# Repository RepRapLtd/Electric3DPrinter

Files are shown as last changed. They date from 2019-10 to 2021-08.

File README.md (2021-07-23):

The RepRap Ltd Electric 3D Printer
==================================

This document is a log of a RepRap Ltd ongoing research project to create a completely new type of 3D printer invented by [Adrian Bowyer](https://reprapltd.com/about/) (to whom “I” below refers…).

(All the images here are in the Pix directory of this repository.)

The Initial Invention (25 July 2019)
------------------------------------

The invention combines three ideas to make a fourth.  The three are:

1.  The [reverse-CT scan 3D printing technique](https://3dprintingindustry.com/news/uc-berkeley-researchers-develop-a-projection-based-3d-printer-from-ct-scans-148274/) from Berkeley and Lawrence Livermore,

2.  The [open-source electric 3D scanning technique](https://www.crowdsupply.com/mindseye-biomedical/spectra) for 3D reconstruction from Spectra, and

3.  [Electropolymerisation](https://www.sciencedirect.com/topics/materials-science/electropolymerization).

My overall synthesis of the three is to use an electric current to make a liquid plastic monomer polymerise to a solid in such a way that it forms a 3-dimensional object with a specified shape, and to do that with a single scan in a time of (I hope…) a few seconds.  Let me start by describing the three precursor technologies in more detail:

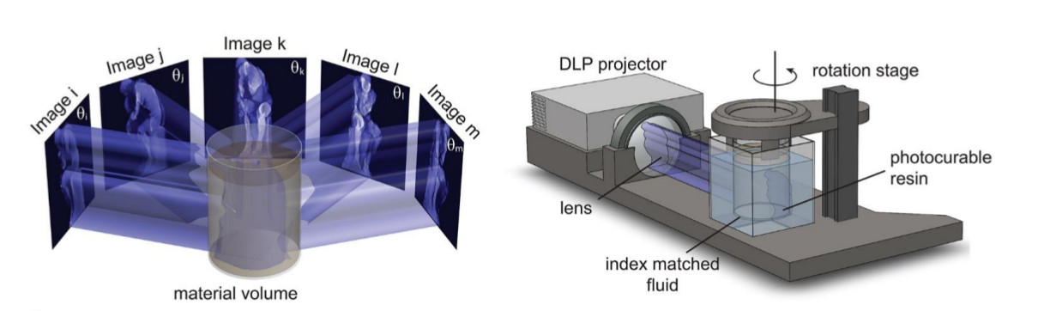
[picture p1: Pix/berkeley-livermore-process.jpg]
Berkeley Livermore Process


The Berkeley/Livermore system [thanks to [B. E. Kelly et al., *Science* 10.1126/science.aau7114 (2019)](https://science.sciencemag.org/content/363/6431/1075)].

Firstly, the Berkeley/Livermore system.  What they do is to shine a light pattern from a digital projector into a bath of liquid monomer that contains a photoinitiator.  Where a sufficient intensity of light falls, the monomer polymerises to form a solid.  So far this description is like a conventional low-cost SLA system; but the really clever bit is that they treat the 3D object to be printed as if it were a CT scan.  The light field is modulated in intensity as if it were (for example) X-rays passing through a patient on a scanner, and they rotate the scan so that ***a complete solid is formed in a single rotation in a matter of seconds***.  Computing the CT-scanner [Radon Transform](https://en.wikipedia.org/wiki/Radon_transform) of a 3D-printing STL file is mathematically and computationally straightforward (it’s essentially just like ray-tracing for computer graphics).  Neatly, their system does not need allowances to be made for refraction as the light enters the transparent rotating cylindrical bath containing the liquid monomer, because they submerge that in another bath that is rectangular, and so has flat faces for the light to pass through.

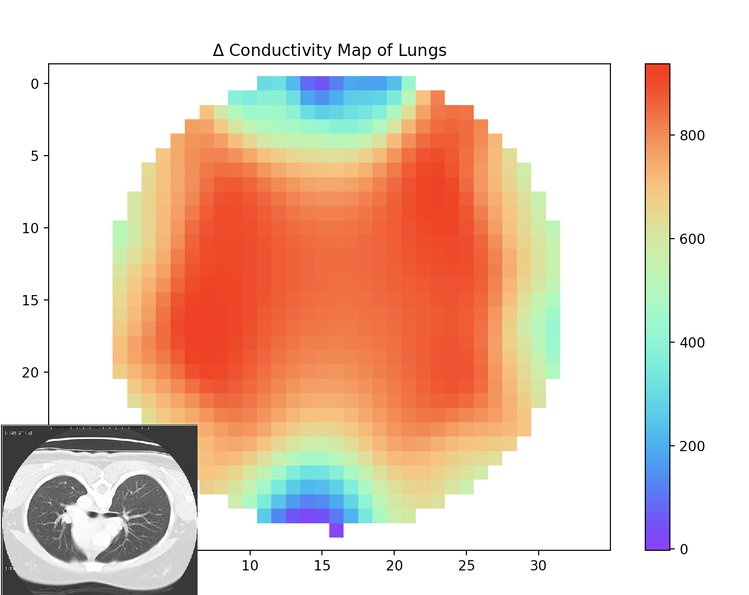
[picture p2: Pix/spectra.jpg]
spectra


A preliminary scan of lung cross-section by the Spectra system [thanks to the [Spectra Crowdfunder page](https://www.crowdsupply.com/mindseye-biomedical/spectra)].

Secondly, the Spectra system. This is an alternative way of CT scanning that does not use X-rays, but instead uses electric current.  What they do is to place the object to be scanned in a bath of conducting liquid, and then apply a voltage from two small point-like electrodes on opposite sides of it and measure the current.  The current takes multiple paths through the liquid around and through the object to be scanned, of course.  But they then rotate the electrodes and repeat the measurement from a slightly different direction, just like rotating the X-ray source and the opposite detector in a conventional CT scanner.  By repeatedly doing this they can gather enough information to construct a cross section of the object being scanned.  By moving the electrodes at right angles to the cross section by a fraction of a millimetre and repeating the process they can make a stack of scans to digitise the scanned object as a full 3D solid.  In practice more than two electrodes are used, and the current is switched electronically between them; this reduces mechanical complexity and increases speed.

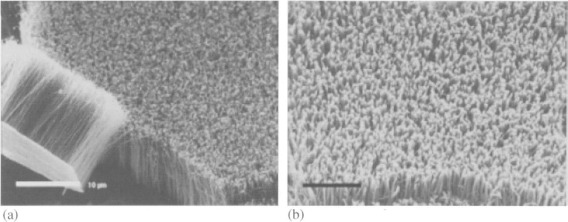
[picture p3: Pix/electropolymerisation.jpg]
electropolymerisation


Nanowires made on a surface by electropolymerisation; scale bar is 10 μm [thanks to the [Science Direct article on electropolymerisation](https://www.sciencedirect.com/topics/materials-science/electropolymerization)].

Thirdly, Electropolymerisation.  The clue here is in the name – this is causing a liquid monomer to polymerise to a solid by passing electricity through it rather than light (or other forms of energy).

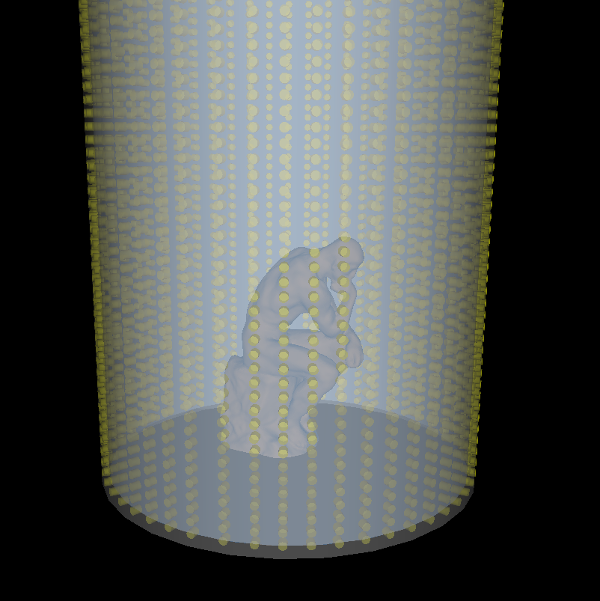
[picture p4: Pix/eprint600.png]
eprint


The Electric 3D Printing system proposed here.

I hope you can now see how these three concepts could work together.  My idea is to have a bath of monomer engineered to polymerise using an electric current.  In place of shining light through it like the Berkeley/Livermore system, the current is programmed using the reverse of the Spectra system.  In its final form (shown in the diagram above), one would have a cylindrical bath containing the liquid monomer.  The walls of the bath would have a fine array of electrodes in a square grid over their entire area (the grid would be finer than in the diagram).  These would be addressed by a controlling computer to pass electric currents through the liquid monomer in such a way as to solidify it just where required to form the 3D solid defined by an STL file (as in conventional 3D printing).  ***The machine would have no moving parts***, and the solid would be formed in (I hope) a few seconds.

The entire machine could, of course, be printed in a conventional two-filament RepRap if [one filament were conducting](https://3dinsider.com/conductive-filament/).

The primary purpose of [the blog post of which this is a copy](https://reprapltd.com/electric-3d-printing/) is to get my ***Electric 3D Printing*** idea out as open-source, and to establish it as prior art so that it cannot be patented.

Finally, and very speculatively, an even more ambitious possibility would be to move from organic chemistry to inorganic, and to replace the bath of monomer with an electrolyte such as copper acetate or copper sulphate.  It might then be possible to cause the copper to precipitate at any location in 3D space if the pattern of electric currents through the liquid could be got right.  The dense copper would settle out of solution, of course, so the process would have to start at the bottom of the bath and work up. I think that this idea would be much more difficult to make work than the polymerisation one.  The reason is that I expect that the polymerisation system would turn out to rely on engineering a non-linear response in the polymerisation reaction to current: probably something like a sigmoid function. That would be very difficult (or even impossible) to do with metal deposition, which is a strictly linear Avogadro’s-number-and-coulombs phenomenon like electro-plating.

But if it could be made to work, we could then 3D-print a complete solid copper object at room temperature.  Or, for that matter, a titanium one…

* * * * *

2 Dimensional Simulation (1 August 2019)
----------------------------------------

TL;DR: The simulation below works and gives sensible predictions. It has thrown up a problem that needs to be solved.

To try this out I decided to start by simulating it, which is to say I’ve written a mathematical model of the process to see if it’s possible to print shapes electrically in theory before going to the trouble of building an actual machine.  The model has (unsurprisingly) some simplifying assumptions:

1.  Start with a 2D disc in the [*x, y*] plane, not a 3D volume in [*x, y, z*], and so see what happens for a single ring of electrodes that form a slice through the cylinder.

2.  Assume the conductivity of the liquid monomer doesn’t change when it sets solid.

3.  Assume that whether a node sets solid or not is decided by the total charge that moved through it for the entire process.

The model does not start with a shape that is to be printed and try to work out the pattern of voltage changes that would need to be made to create that shape.  This would have to be done for the actual machine, but – before doing that – I decided just to apply patterns of voltages that seem as if they might make something sensible (like a cylinder in the middle) and see what they would actually do.  This is much simpler than doing the backward calculation from the final desired shape.

Let V be the potentials over the disc, and E be the field.  Then Laplace’s simplification of Poisson’s partial differential equation (P.D.E.):

<div align="center">∇<sup>2</sup><em>V</em>=0,</div>

when solved gives <em>V</em>, and <em>E</em> can then be found from

<div align="center"><em>E</em>=−∇<em>V</em>.</div>

The current through any node will be proportional to the magnitude of the vector *E* at that node.  Integrate that current over the time of the whole simulation, and you have the total charge that has run through that node, which should decide if it sets solid or not.

I wrote a finite-difference C++ program to solve for*V* over a disc.  You can get the code [from Github here](https://github.com/RepRapLtd/Electric3DPrinter); please let me know of any bugs you find.  The obvious thing to do with a disc is to use the polar form of Laplace’s equation as the basis of the solution.  But the problem with that is that angular resolution decreases with increasing radius unless you insert extra nodes, which makes things complicated.  So I decided to use a rectangular Cartesian grid instead, and to code the disc in the boundary conditions.

In their simplest form those boundary conditions consist of a circular perimeter perpendicular to which the gradient vector, *E,*is forced to be 0 (which is to say that no current flows through the walls).   Added to that are a couple of point electrodes diametrically opposite each other, one of which is at a positive voltage, and the other is negative.  At these current does flow. Here is the solution for *V* over the disc for that situation on a 50×50 grid of nodes:

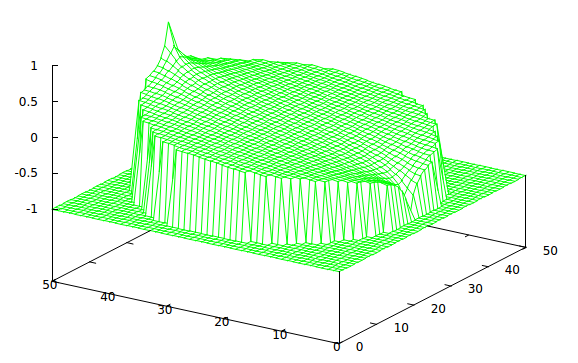
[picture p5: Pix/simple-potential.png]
simple-potential


Potential, *V*, over the disc

The numbers don’t mean much – the picture would look the same but for scaling with 100 volts as with 1 volt.  The flat area is outside the disc and can be ignored.  The peak and the valley are the positive and negative electrodes, and the rest of the grid is the potential everywhere else.   Taking the partial derivatives of *V* at each node with respect to *x* and *y* gives the vector *E* at that node.  Pythagoras then gives the magnitude of *E*:

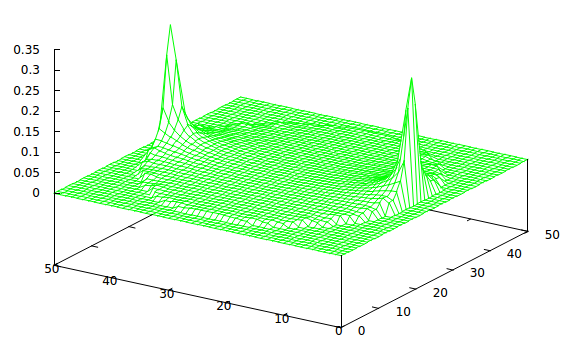
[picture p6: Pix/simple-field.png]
simple-field


Field magnitude, |*E*|, over the disc.

As mentioned above, the current flowing through each node will be proportional to the value of the magnitude of *E* at the node.  The currents are, as would be expected, greatest at the electrodes.  But I was encouraged by the slope in the middle of the plot of the potentials, which corresponds to the non-zero plateau in the middle of the field magnitude plot.  I thought that if one were to pass a series of currents from the electrodes as they were energised round the circle the sum of charges in the middle might exceed that at the individual electrodes, and so one would have built a solid disc in the middle and left liquid monomer round the outsides.  Unfortunately, this did not happen.  Here is the result of energising twenty pairs of electrodes in sequence and integrating the currents flowing through all the nodes for each one:

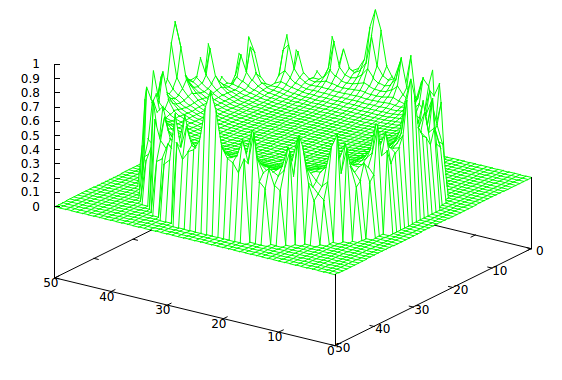
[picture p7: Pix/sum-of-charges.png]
sum-of-charges


Integral of the current from twenty electrodes energised sequentially round the disc.

The jagged periphery is an aliasing effect from the grid, and doesn’t matter at this stage.  As you can see there is a substantial charge plateau in the middle, but unfortunately it is still exceeded by the sums of the currents at the electrodes, even though 18 of them will be switched off for each individual energising.  This means that the machine would tend to get clogged solid at the electrodes, regardless of what was going on in the middle.

This is discouraging.  But it is only the simplest possible simulation of the simplest possible pattern of currents.  There are many variables that I have not altered, such as different voltages at different electrodes (they don’t all have to be either off or on), different persistence times for one pattern, *V*, and fading dynamically between voltage patterns at the electrodes.  Now I have the basic simulation written all these will be easy to experiment with.

If these experiments can be made to produce more hopeful results, then I will change the simulation to full 3D rather than the 2D disc.  This is straightforward as it just means adding a*z* term to the P.D.E. along the cylinder axis and then solving in the entire cylindrical volume, rather than just a disc slice of it.  Visualising the results will be rather like visualising a CT scan – a solid contour in the volume of constant charge integral would be triangulated and plotted in 3D.

* * * * *

2 Dimensional Simulation of Actual Printing (10 August 2019)
------------------------------------------------------------

TL;DR: The simulation now “prints” simple shapes.

Obviously (after two days of thought…) if the machine prints solid where you don’t want, and doesn’t print where you do want, then all that is needed is to invert the process.  In other words we need a polymer in which polymerisation is inhibited or reversed by electricity.

Remember Loctite:

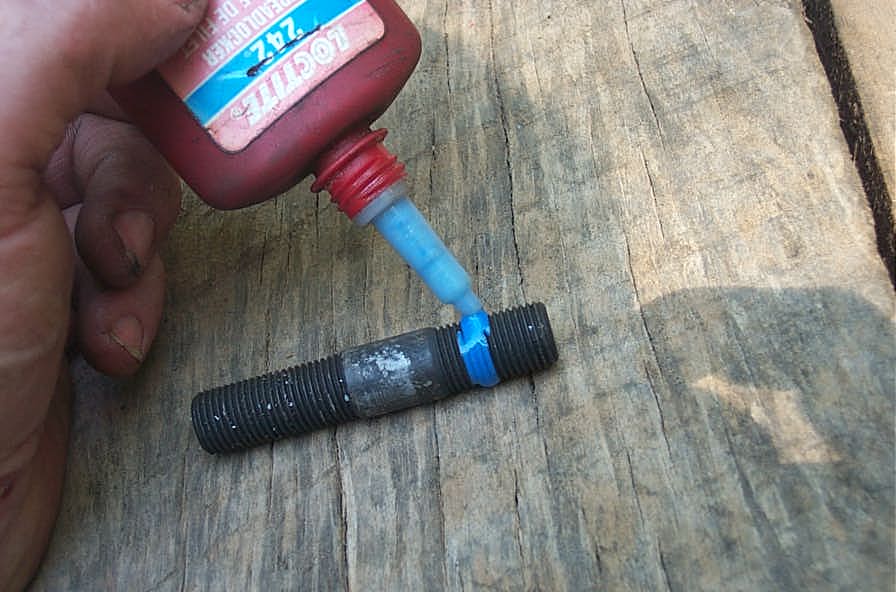
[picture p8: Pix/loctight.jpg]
loctight


This is a remarkable material that polymerises solid except in the presence of oxygen, which keeps it monomeric.  Thus when you tighten a nut and bolt with liquid Loctite on the threads this excludes the oxygen, solidifies the Loctite, and locks the nut to the bolt.  Loosen them a bit to allow the oxygen back in, and the polymer depolymerises back to a liquid, and the threads can be undone easily because the reaction is also reversible.  (The – possibly apocryphal – story is that Vernon Krieble, the inventor of Loctite, had greater difficulty making a bottle that would allow oxygen to permeate in to keep the stuff liquid than he did making Loctite itself.)

Let’s suppose that we can make a monomer that behaves like Loctite, but in which electricity takes the place of oxygen.  Pass a current through it and it liquefies; turn it off and it solidifies. This would be useful stuff in its own right, but it would also be an ideal material for the electric 3D printing idea here.

The transition from solid to liquid with charge integral would not be instant.  For this simulation I propose a sigmoid function, as I mentioned above:

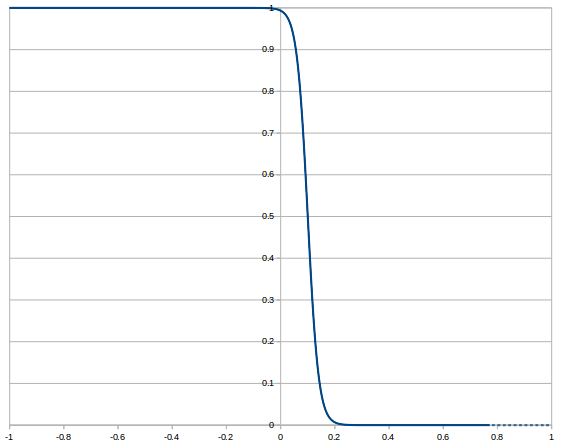
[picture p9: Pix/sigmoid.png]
sigmoid


 *f*(*x*)=1–*e*<sup>*a*(*x–b*)</sup>/(*e*<sup>*a*(*x–b*)</sup>+1)

Ignore the negative bit of the abscissa; that’s just there for me to check things are correct; you can’t have negative charge integral just as you can’t have -3 apples. The variables *a* and *b* alter the shape and offset to the right of the sigmoid function and can be played around with in the simulation to experiment, or maybe one day to match the characteristics of a real polymer.  The charge integral (the last surface plot above) was normalised to lie in the range [0, 1].  That is the value of *x* in the sigmoid function.  The vertical axis is degree of polymerisation: 0 charge gives solid, and the (at the moment hypothetical) material liquifies as charge integral increases to the right, going fully liquid at a value around 0.2.  Note at this stage these numbers aren’t real coulombs; they would be, however, proportional to real coulombs in a real machine. (The values *a* = 50 and *b* = 0.1 were used for this, incidentally.)

As with the last surface plot above, if we put 1 “volt” on each electrode round the circle in turn, along with -1 “volt” on the diametrically opposite electrode, we now print this:

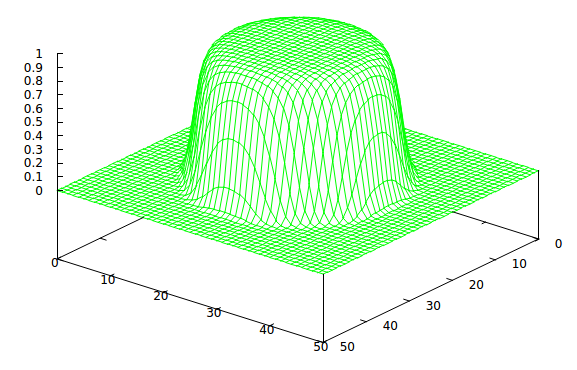
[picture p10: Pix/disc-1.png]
disc-1


It’s solid in a circle in the middle, and liquid all around.  We’ve printed a disc!  Remember that the height of the surface from 0 to 1 represents the degree of polymerisation of the monomer – higher means more solid.

Now here’s what happens if we just put 1 “volt” on a quarter of the electrodes adjacent to each other and -1 “volt” on those diametrically opposite them:

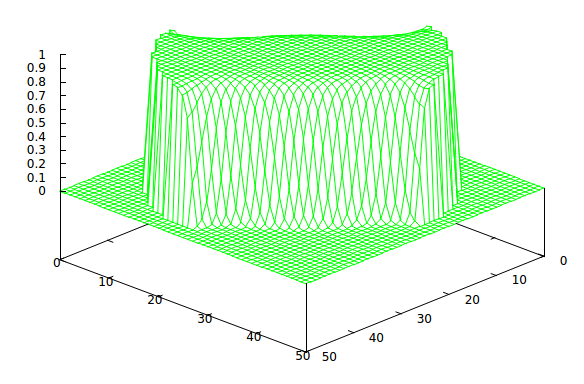
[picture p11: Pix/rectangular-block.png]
rectangular-block


We’ve printed a (roughly) rectangular block.

I think it’s time to move the simulation from a 2D disc slice through the machine to a 3D cylinder that represents the entire machine.

* * * * *

3 Dimensional Simulation (13 August 2019)
-----------------------------------------

The simulator now solves for Laplace’s equation in 3D.

Here’s the result of running round the bottom of the cylindrical reaction vessel in a circle putting 1 “volt” on each electrode and -1 “volt” on the opposite one, and moving up one level in Z then repeating that for the next ring of electrodes all the way up to the top.  The transparent cylinder is the reaction vessel itself (without the electrodes for clarity):

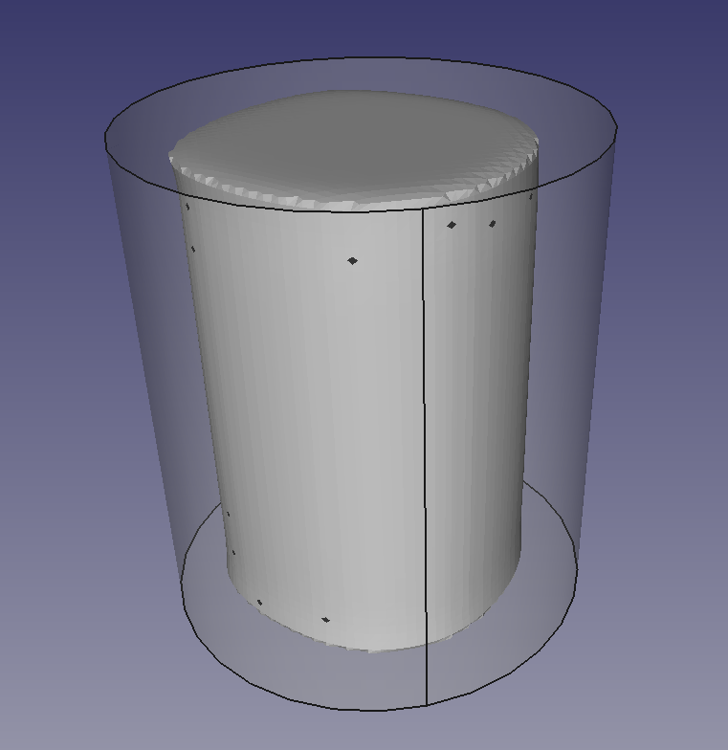
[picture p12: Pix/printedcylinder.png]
printedcylinder


It’s printed a cylinder!

Sorry for the odd flaky triangle in the image (to be fixed).  Converting the accumulated charges to a 3D model relies on  [Dominik Wodniok’s implementation of Marching Cubes](https://github.com/RepRapLtd/dualmc) for it’s output, incidentally, so big thanks to him.

* * * * *

The Effect of More Voltage or Longer Accumulated Charge (13 September 2019)
---------------------------------------------------------------------------

I ran a series of tests to make cylinders like the one above, increasing the voltage applied to the electrodes, which we would expect to reduce the diameter of the resulting cylinder.  Here is the result:

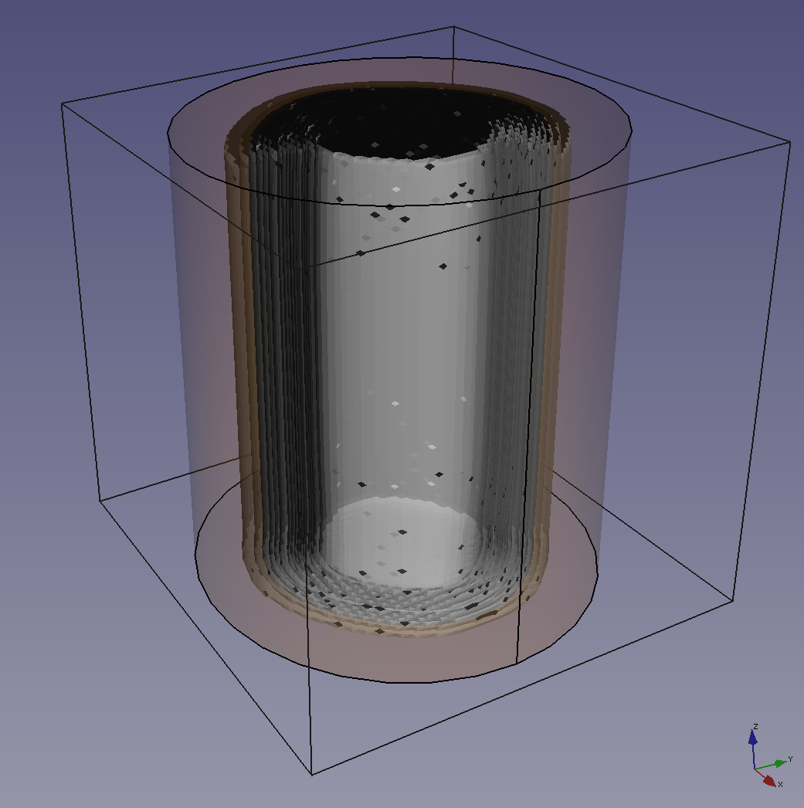
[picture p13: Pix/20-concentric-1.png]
20-concentric


The outer box surrounds the 50x50x50 node finite-difference PDE solution grid, and the transparent cylinder is the modelled tank of the machine (outside that there is no voltage, no current, and no 3D printing material).  The tank is 44 nodes in diameter.  In the middle are 20 concentric separately-printed cylinders all superimposed for comparison.

Each cylinder is printed by applying +V and -V to a pair of diametrically opposed electrodes at the bottom then rotating that pattern round the bottom disc.  The same thing is done for each disc upwards 50 times until the top is reached.  The accumulated charge at each node from doing all that is calculated and then subjected to the sigmoid function (see the 10 August log above).  The result is one printed cylinder.

That was done 20 times, increasing the value of V from 1 to 20.

All the units are arbitrary, of course; Laplace’s equation doesn’t know anything about the difference between 1 mm and 1 cm, and 1 volt or 10 volts; as long as things were consistent, the pattern would be the same.  But, for sanity, let’s say that the nodes are 1 mm apart, and that when V = 1 that is 1 volt.  We can then plot the radii of the resulting cylinders against applied voltage, V:

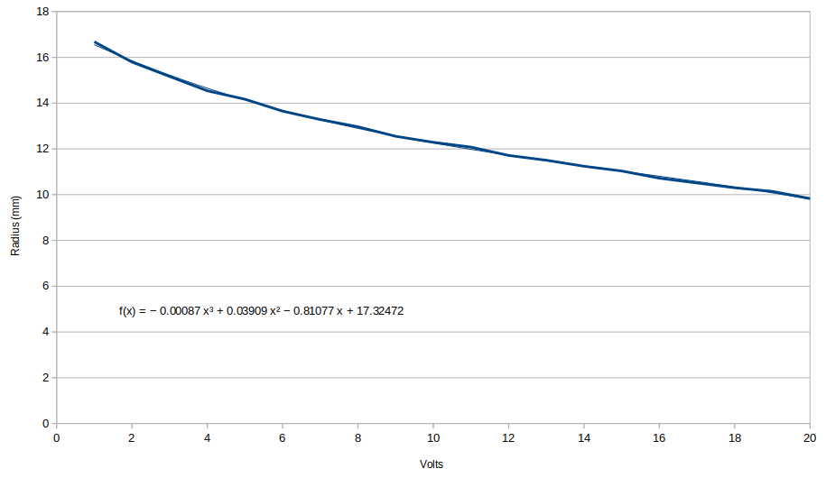
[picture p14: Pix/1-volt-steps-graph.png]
1-volt-steps-graph


The result is not linear, unsurprisingly. But equally it is not all over the place, implying there will be a smooth radius reduction with increasing voltage.  The cubic equation on the graph is a best fit (the thin, barely visible, line on the graph).  There is no physical reason to expect a cubic (or any other polynomial) relationship between radius and voltage; I just wanted an empirical equation that could be used for prediction over the experimental range when it comes to trying to make more complicated shapes.

The title of this log entry says “More Voltage or Longer Accumulated Charge”.  As with length and voltage, time units are arbitrary. But imagine that +/-1 volt is applied to each pair of electrodes for 1 second before stepping on.  The result of doing that should be the same as applying +/-0.1 volts for 10 seconds at each pair.  This is because the process is assumed to convert solid to liquid dependent on the integrated charge that each node in the grid sees (a big assumption).  If the material is ohmic (another big assumption) and its resistance doesn’t change when its phase changes (a further big assumption), then this will be the case.

Finally in this log entry, a word about data processing.  The result of solving the PDE is a tensor of accumulated charges at each node.  These are put through the sigmoid function to see if they will be solid or liquid (or some sort of sticky half-way state), which results in another tensor of values: 1 for solid, 0 for liquid, and fractions for sticky-in-between.  Those are written to a file.  The [marching cubes algorithm](https://en.wikipedia.org/wiki/Marching_cubes) is then run over that tensor of values to create a triangulation of the imagined solid surface.  That triangulation is written out as an STL file, which can then be loaded into [FreeCAD](https://www.freecadweb.org/) and displayed, as above.   With a little triangulation repair we could even print it on a conventional RepRap…

Our version of marching cubes is [here on Github](https://github.com/RepRapLtd/dualmc), and the C++ code for solving the PDE [is here](https://github.com/RepRapLtd/Eclipse/tree/master/workspace/Electric3DPrinter) (along with a lot of the experimental data presented in this log).

* * * * *

First attempt to print a controlled shape (8 October 2019)
---------------------------------------------------------

If we want to print a shape, one of the things it would be useful to know is the inverse of the graph immediately above.  That is to say, given a radius, what voltage should we apply to achieve it?  This is the inverse of the above graph together with its fitted cubic which tells us what voltage to apply to get what radius:

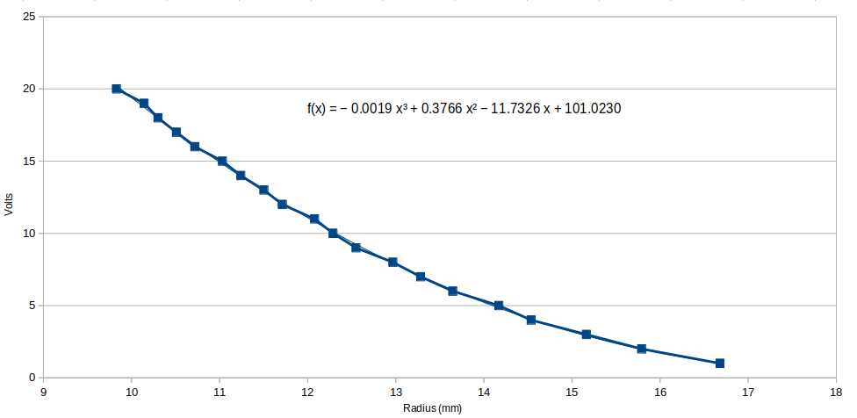
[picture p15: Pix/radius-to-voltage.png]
radius-to-voltage


(Remember: the cubic is just an empirical fit to reproduce the curve; the coefficients have no physical significance.)

Now, as the voltages in the simulation are switched to the ring of contacts round the reaction vessel, the voltage can be set by a very simple ray-trace calculation across an imagined shape in the middle of the vessel – a rectangular block, say.  The ray-trace gives the radius, and the radius gives the voltage to apply.  Here is the simulated printed result:

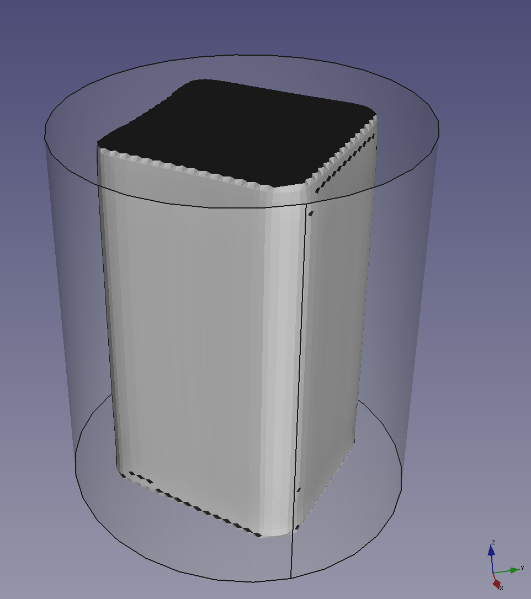
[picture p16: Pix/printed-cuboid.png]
printed-cuboid


It prints, as requested, a rectangular block (the transparent cylinder is the reaction vessel, as before).  The original block that was ray-traced had a square cross section 27x27x50 mm.  The printed block is 25.5×25.5×50 mm.  The slight reduction in size is possibly due to a cross-talk effect between higher and lower voltages, and layers influencing other layers above and below them.  But the block’s faces are remarkably flat.  The rounded corners are not a surprise, particularly given that the simulation only had a 50x50x50 node grid.

The block that was ray-traced then printed above was the entire height of the reaction vessel.  Here is what is obtained if it is made shorter: 36mm high, placed 7mm up from the base of the reaction vessel, together with a 10mm diameter cylindrical stalk in the centre (which is rather like the support in conventional 3D printing needed to hold the object in place):

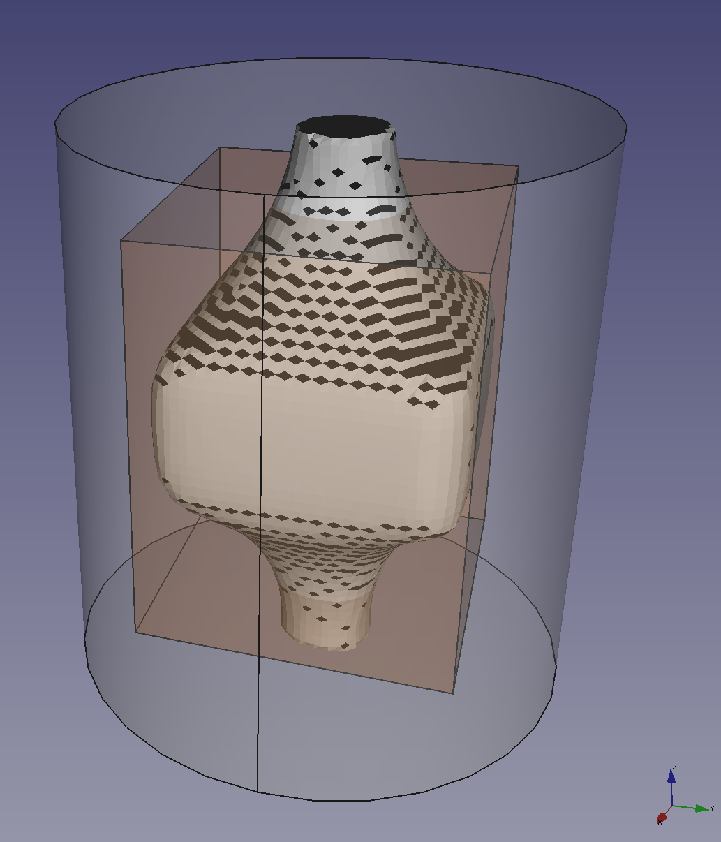
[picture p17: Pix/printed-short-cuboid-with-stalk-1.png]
printed-short-cuboid-with-stalk


The original rectangular block that was ray-traced to create this is shown in transparent orange.  As you can see, I still haven’t fixed the occasional dud triangle in the marching cubes program…

As you can also see, the effect of the high currents needed to reduce the diameter to that of the stalk top and bottom has been to erode the desired block as well.  In addition, the comparitively low currents required for the rectangular block have meant that the stalk-cylinder gets fatter where it joins the block.  In short, because the currents can flow freely in 3-dimensional space, there is a lot of vertical interference when trying to print in layered discs.

But, of course, with this method of 3D printing there is no need for, nor advantage to, treating the objects to be printed in layers.  Any pattern of voltages can be applied anywhere over the surface of the cylindrical reaction vessel, and I have not tried using that extra freedom at all yet.

I think that will be the next step.

* * * * *

Printing random(ish) shapes and deep learning (23 July 2021)
------------------------------------------------------------

After a year-and-a-half gap (caused, inter alia, by the covid pandemic) I have come back to the Electric 3D Printer. I've set it up to "print" random shapes in a way I shall immediately describe. But what use are random shapes? They can be used to train a neural network to generate shapes that are not random automatically. I shall outline my proposal for that at the end of this section.

I have written a Python wrapper for the C++ P.D.E. solver that works out the printed shapes. It's in the **Software/GAN** directory of this repository.

What it does is to generate a list of pairs of electrodes on the cylindrical boundary of the reaction vessel of the Electric 3D Printer and then assign random voltages to each pair. These are then fed into the solver, and the output of that is read back into the Python program to be subjected to the marching cubes algorithm to see what the pattern prints. The system now uses the standard Python version of marching cubes, **import mcubes**, to generate the shapes from the charge integrals, which works a lot better, incidentally.

Here is an example of the sort of thing that results; a lumpy cylinder:

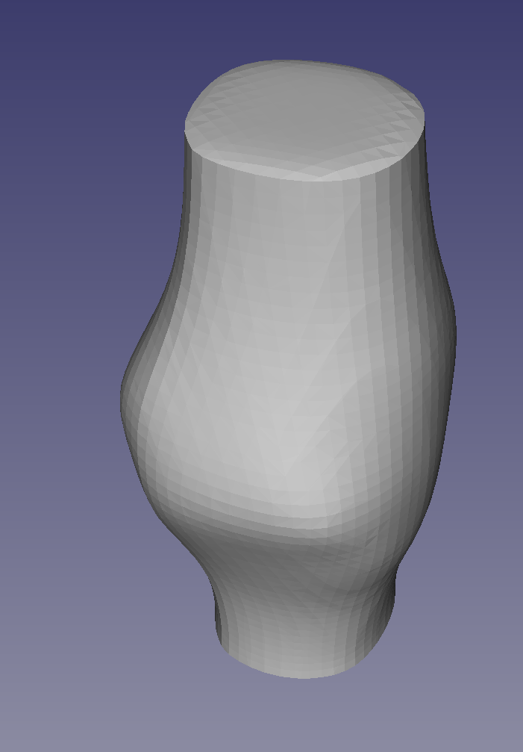
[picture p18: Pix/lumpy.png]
lumpy-cylinder


For this the pairs of electrodes were distributed at random. To get an idea of what's going on here's another run with fewer random electrode pairs:

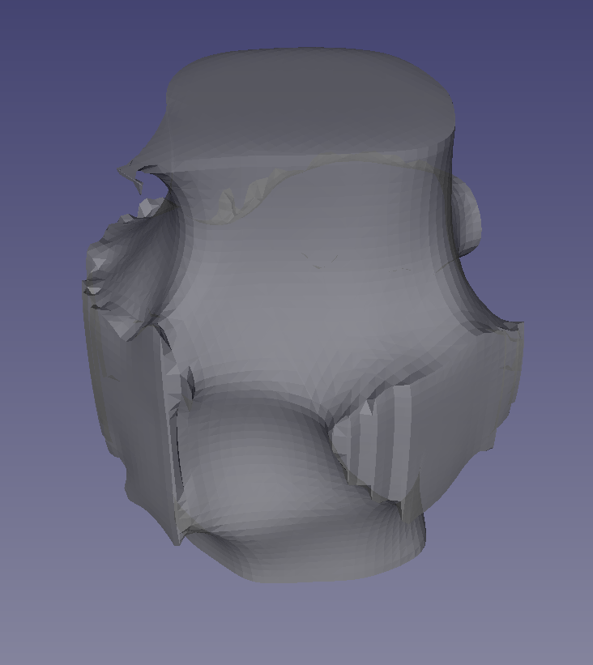
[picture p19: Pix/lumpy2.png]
lumpy-cylinder2


And here is the same shape with a set of straight lines superimposed on it that join the pairs of electrodes that created it:

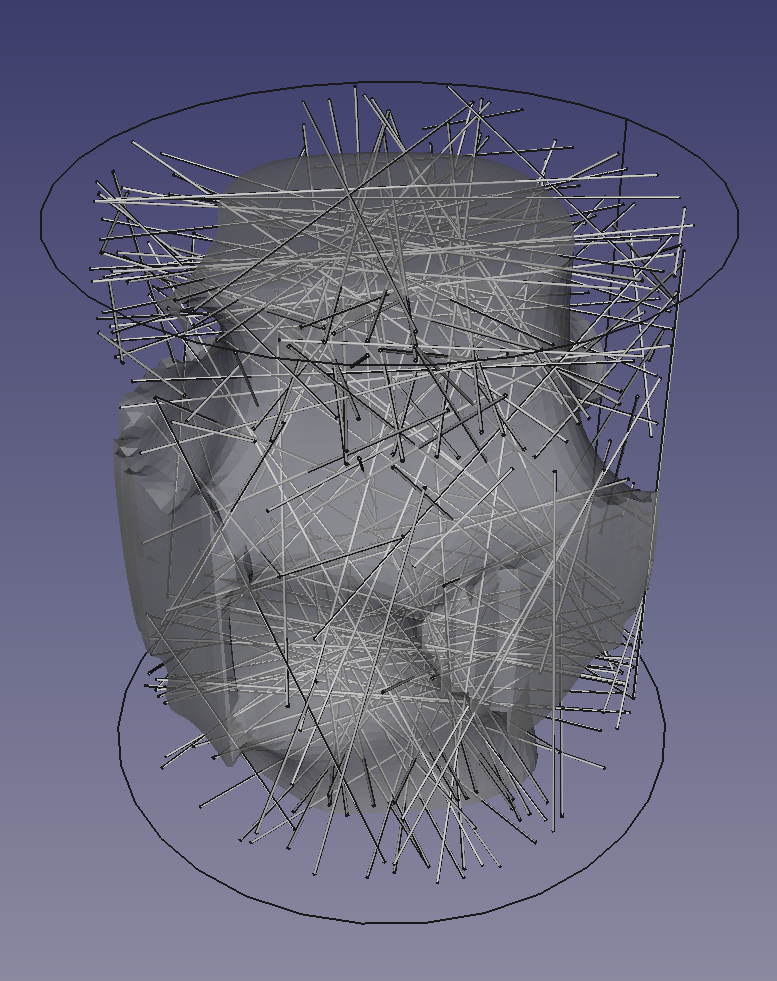
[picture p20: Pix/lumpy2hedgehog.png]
lumpy-cylinder-hedgehog


Because fewer electrodes were used, and consequently less current was passed through the volume, more of the shape has remained solid, in some cases right out to the boundary.

But why do we get a cylinder-like shape extending the length of the reaction chamber? In part, this is because that's the shape of the chamber, and what we're doing is to erode away inside it. But also, consider a slice across the cylinder to make a disc:

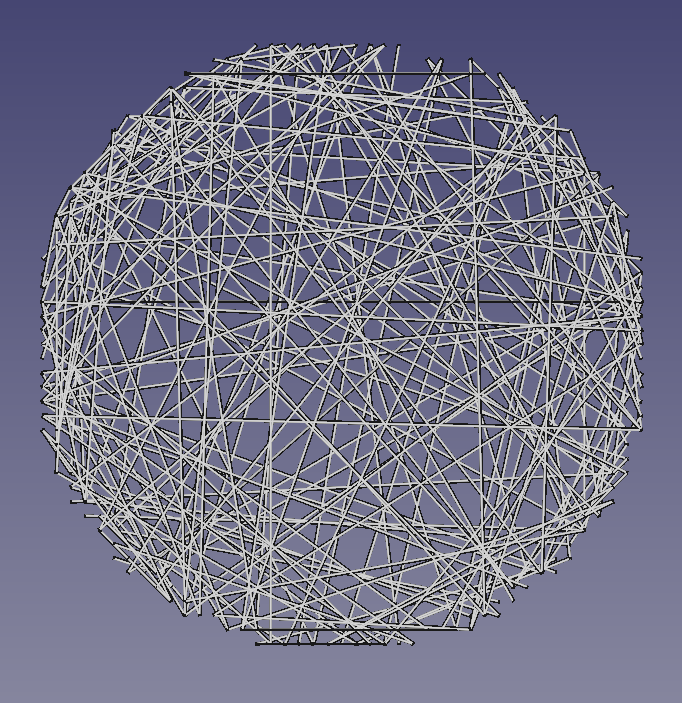
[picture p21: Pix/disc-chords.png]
disc-chords


If we choose 100 pairs of random points from the uniform distribution over the disc's circumference then draw the chords between them, this is what we get. As you can see, the density round the edges is higher than in the middle for the intuitively obvious reason: a random pair of points are not all that likely to be more or less diametrically opposite each other. This is what's going on in three dimensions as well, and is another reason that we tend to make roughly cylindrical shapes in the middle.

But we don't just want to make cylinders and prisms. The physics of the process is introducing a bias into the process and, if we can quantify that bias, we can apply its inverse in an attempt to correct it. In fact I have started to do that in the two solids at the start of this section. The electrode pairs were not chosen from the uniform distribution over the surface of the cylindrical reaction chamber. They were biased towards the top or bottom - this is the reason that the solids have bulges around half way up the cylinder - and biased to be more likely to be near to diameters than random chords would be.

It is easy to generate pseudo-random numbers from any distribution you like. You just integrate the distribution function to get the corresponding cumulative distribution function (CDF), then invert this to get random points from the desired distribution. That is to say you feed uniformly distributed random numbers into the y axis of the CDF and the resulting x values will be from the desired distribution.

I shall shortly add a couple of functions to the Python program that generates the voltage patterns to allow any distribution to be specified by points along it. Simpson's Rule will then be used to make the CDF, and the inverse of that will give the randomness required. The aim will be to print random blobs in the middle, not cylinders.

When all this is working we will have a means to train an ordinary neural network to generate the pattern of voltages needed to print a given input shape. But it should also be possible to use that to make a [Generative Adversarial Neural-Network](https://realpython.com/generative-adversarial-networks/) to create all sorts of useful engineering shapes automatically.

How will the first stage work? We can generate random input patterns (the pairs of charged electrodes), and we know the shape of the result (the output of the C++ program that solves the P.D.E.). What we want for a given output shape (an STL file, say) is to know the pattern of electrode voltages that will create it. So we can make a training data set as big as we like, albeit random, and hope that a network trained on it will be able to make regular shapes as well.

The next stage is to get the voltage distributions right to make blobs, not cylinders, then we will move on to the neural network training.

* * * * *

References and Bibliography
---------------------------

B. E. Kelly *et al*., Volumetric additive manufacturing via tomographic reconstruction, [*Science* 10.1126/science.aau7114 (2019)](https://science.sciencemag.org/content/363/6431/1075)

Spectra Scanner Documentation [https://openeit.github.io/docs/html/index.html](https://openeit.github.io/docs/html/index.html)

Jianfeng Ping *et al*., Adhesive curing through low-voltage activation, [*Nature Communications* volume 6, Article number: 8050 (2015)](https://www.nature.com/articles/ncomms9050.pdf)

* * * * *

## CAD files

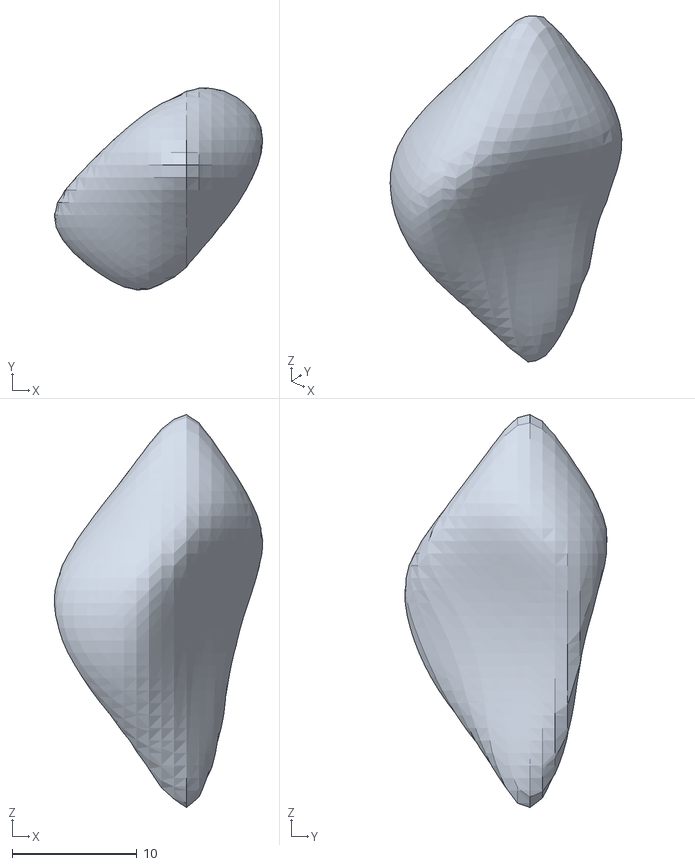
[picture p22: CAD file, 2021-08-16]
Software/GAN/t2.obj
16.7 x 16.2 x 31.5

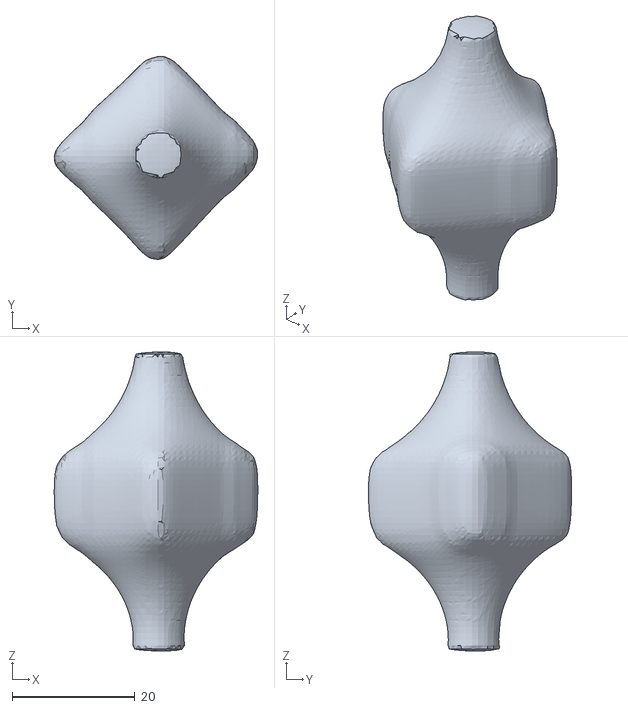
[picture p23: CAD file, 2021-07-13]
Software/Simulation/file-mediated.stl
33.2 x 33.1 x 48.8

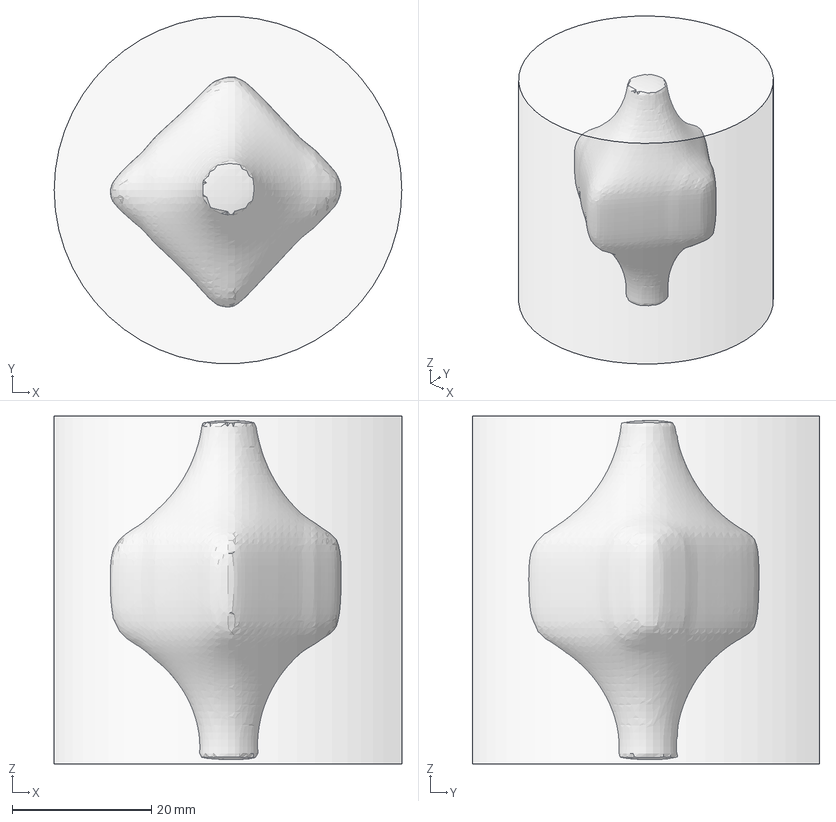
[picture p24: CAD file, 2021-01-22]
Software/Simulation/printed-short-cuboid-with-stalk.FCStd
50.0 x 49.9 x 50.0 mm
tst99_fixed

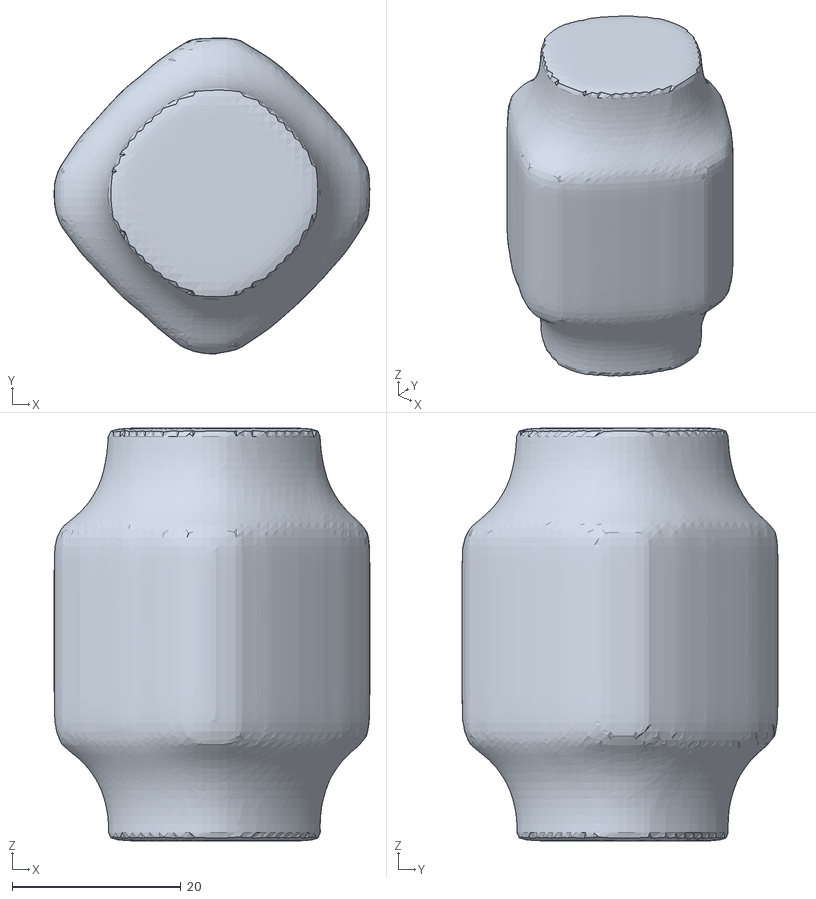
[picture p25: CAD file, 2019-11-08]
Software/Simulation/rp2.stl
37.4 x 37.5 x 49.0

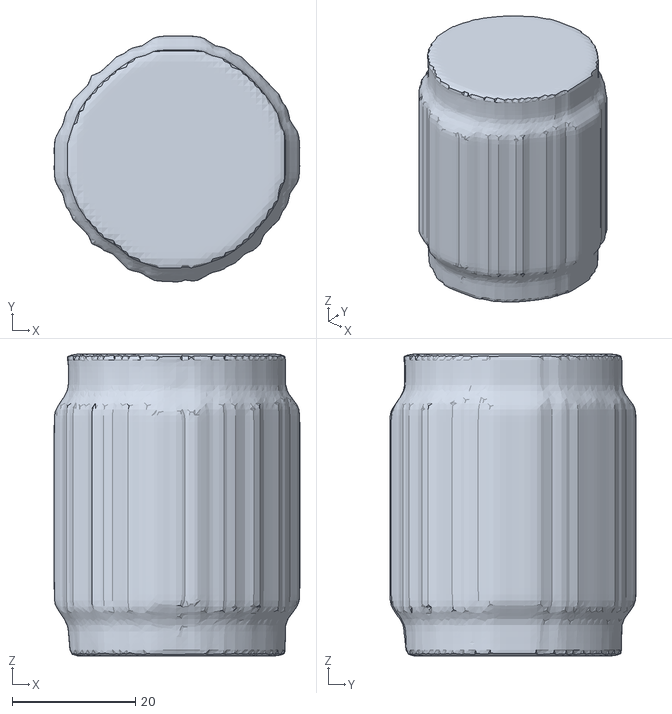
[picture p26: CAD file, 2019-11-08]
Software/Simulation/rp1.stl
39.8 x 39.9 x 49.0

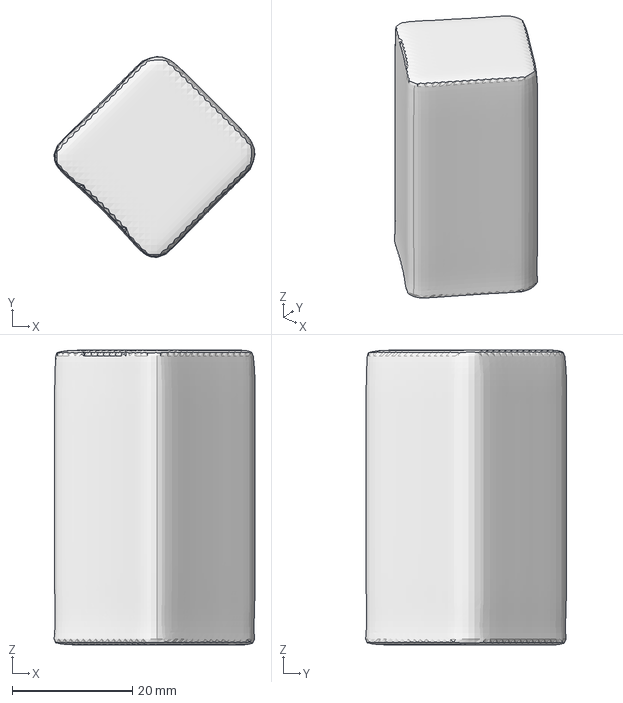
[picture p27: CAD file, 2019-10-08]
Software/Simulation/printed-cuboid.FCStd
33.4 x 33.4 x 49.0 mm

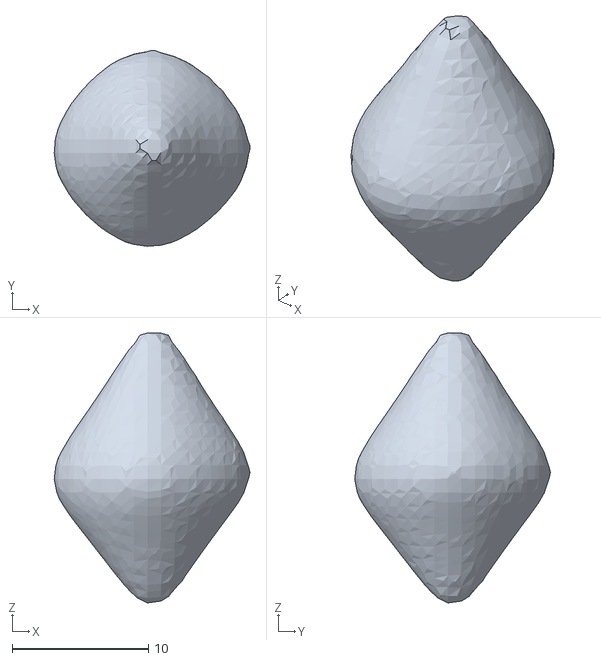
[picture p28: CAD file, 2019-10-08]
Software/Simulation/rectangleAttempt3.stl
14.4 x 14.4 x 19.8

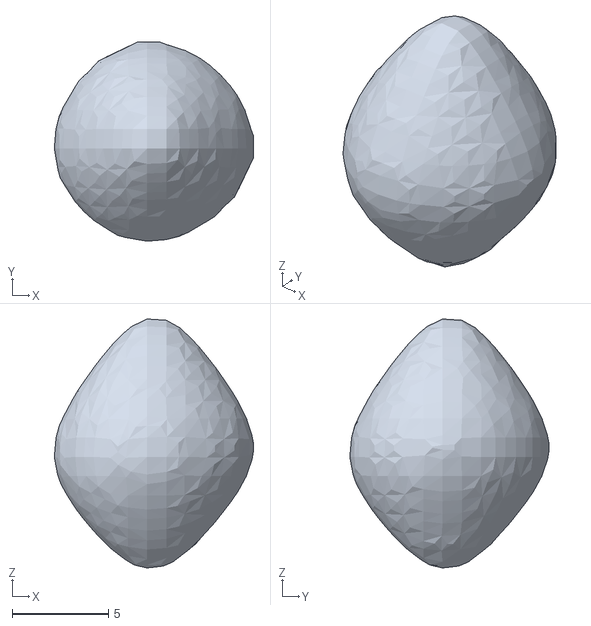
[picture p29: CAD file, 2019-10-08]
Software/Simulation/rectangleAttempt2.stl
10.3 x 10.3 x 12.9

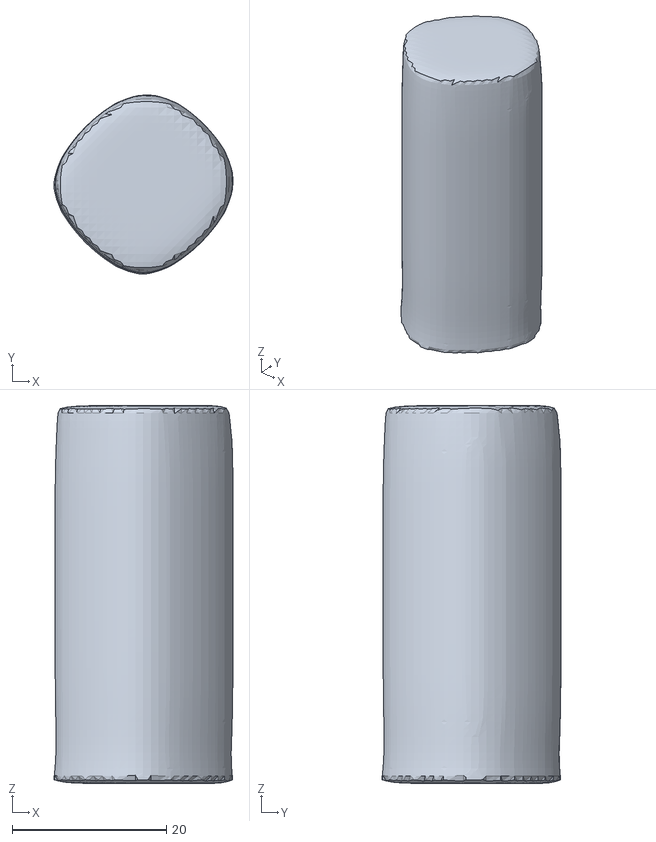
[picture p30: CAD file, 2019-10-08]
Software/Simulation/thresholdTensor-12.stl
23.2 x 23.2 x 49.0

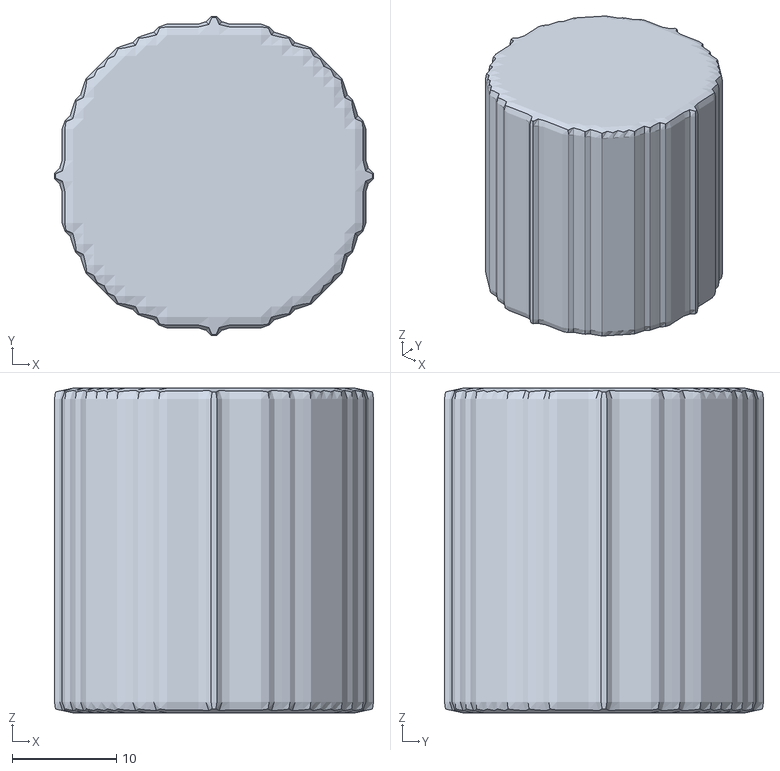
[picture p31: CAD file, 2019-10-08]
Software/Simulation/testCylinder.stl
30.5 x 30.5 x 31.1

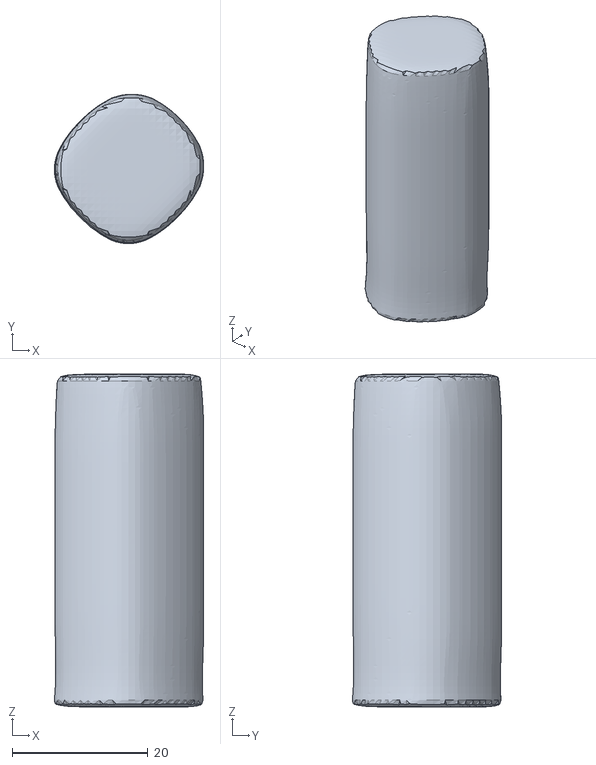
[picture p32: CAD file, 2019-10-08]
Software/Simulation/thresholdTensor-14.stl
22.0 x 22.0 x 49.0

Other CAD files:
Software/Simulation/test13-7-21.stl
Software/Simulation/tst99.stl
Software/Simulation/tst99_fixed.stl
Software/Simulation/rp3.stl
Software/Simulation/rp.stl
Software/Simulation/r4.stl
Software/Simulation/rectangleAttempt.stl
Software/Simulation/cylinders-voltages-coincident.FCStd
Software/Simulation/cylinders-voltages.FCStd
Software/Simulation/thresholdTensor-1.stl
Software/Simulation/thresholdTensor-10.stl
Software/Simulation/thresholdTensor-11.stl
Software/Simulation/thresholdTensor-13.stl
Software/Simulation/thresholdTensor-15.stl
Software/Simulation/thresholdTensor-16.stl
Software/Simulation/thresholdTensor-17.stl
Software/Simulation/thresholdTensor-18.stl
Software/Simulation/thresholdTensor-19.stl
Software/Simulation/thresholdTensor-2.stl
Software/Simulation/thresholdTensor-20.stl
Software/Simulation/thresholdTensor-3.stl
Software/Simulation/thresholdTensor-4.stl
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

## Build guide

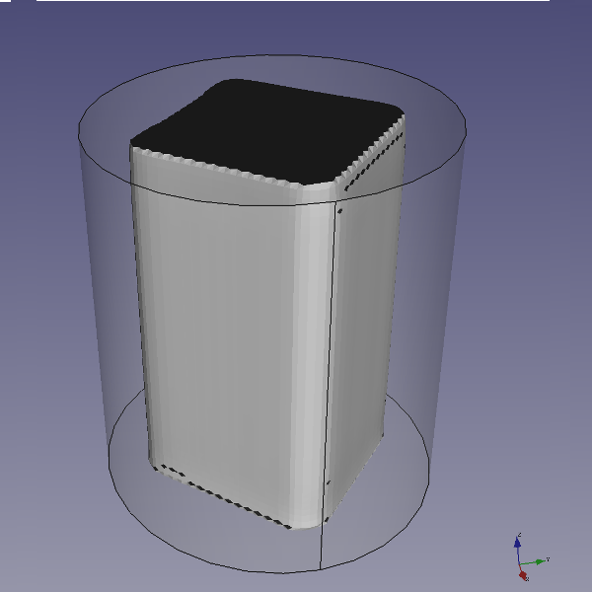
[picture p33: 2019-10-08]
Software/Simulation/Pics/printed-cuboid-600.png

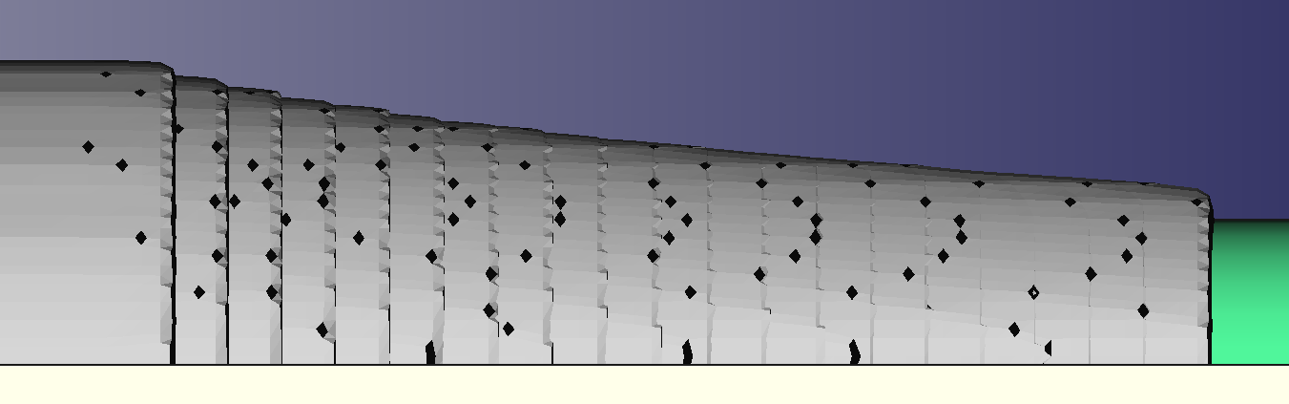
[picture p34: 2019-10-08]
Software/Simulation/1-volt-steps.png

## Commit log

2019-10-08 Sorting out submodules...
    [cylinders-voltages-coincident.FCStd, cylinders-voltages.FCStd, diameter-vs-voltage.ods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]
2019-10-08 First attempt to 'print' a non-cylindrical shape in simulation: a cuboid.
    It worked...
    [diameter-vs-voltage.ods, printed-cuboid.FCStd, rectangleAttempt.stl]
2019-10-08 More experiments on printing ray-traced shapes.
    [printed-cuboid.FCStd, printed-short-cuboid-with-stalk.FCStd, rectangleAttempt2.stl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]
2019-11-08 Added parallelisation of the Gauss-Seidel PDE solution from Mathijs de Boer (https://github.com/Czorio/Electric3DPrinter). Thanks! On my Linux box this gives a speedup from 181 seconds to 84 seconds.
    [r4.stl, rp.stl]
2019-11-08 Relaxation added to the Gauss-Seidel PDE solution, but currently turned off.
    [rp1.stl, rp2.stl, rp3.stl]
2021-01-22 Reverted to last working version in anticipation of doing more experiments.
    [printed-short-cuboid-with-stalk.FCStd, tst99.stl, tst99_fixed.stl]
2021-07-13 Starting work on using a voltage pattern file to generate a shape. Idea is that will be generated by a GAN from a shape description.
    [test13-7-21.stl]
2021-07-13 Now with fewer bugs...
    [file-mediated.stl]
2021-07-13 One fewer bug...
    [file-mediated.stl]
2021-07-15 Started work on GAN to decide input voltage patterns: python marching cubes to interpret .tns files from the simuation.
2021-07-16 Added random voltage pattern generator. Makes any shape you like as long as it's a cylinder... Thought needed on Z distribution?
2021-07-22 Random shapes working. Auto-generated README...
    [t2.obj]
2021-08-03 Modified C++ and Python to allow the sigmoid function to be changed by command line arguments.
    [t2.obj]
2021-08-03 Experimenting with parameters to see how best to erode the ends.
    [t2.obj]
2021-08-13 Random shape generator WIP...
    [t2.obj]
2021-08-16 Tidying Python code...
    [t2.obj]
2021-08-16 Sort of hole drilling function added...
    [t2.obj]
